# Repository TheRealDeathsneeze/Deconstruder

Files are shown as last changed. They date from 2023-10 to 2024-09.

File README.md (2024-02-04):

# Current Status: Experimental

Deconstruder is a toolhead for the voron v0 utilizing the v0.1 carraige and NF crazy, designed around maximizing rigidity while maintaining a small footprint and low mass. No other hot ends will be supported due to some of the unique features of the NF crazy / mosquito hot end, such as the ability to use four bolts on two different planes to secure the hot end to the toolhead, and the ability to carry a 'fan net' or 'mosquito net' at the bottom of the heatsink frame, as well as the built in 2510 mounting saving a fair amount of weight and space over other options. 

[Bill Of Materials](https://github.com/TheRealDeathsneeze/Deconstruder/blob/main/BOM.md)

[Assembly Instructions](https://github.com/TheRealDeathsneeze/Deconstruder/blob/main/assembly_instructions.md)

[Printing guide](https://github.com/TheRealDeathsneeze/Deconstruder/blob/main/STLs/PRINTING.md)

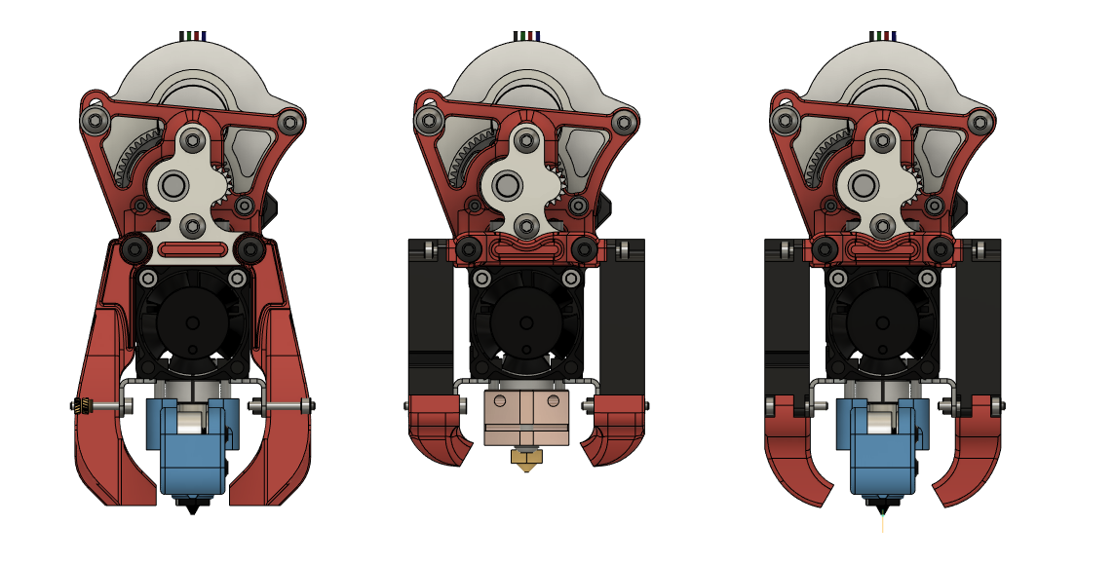
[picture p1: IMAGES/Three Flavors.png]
Deconstruder Types


Deconstruder is the same width in X, and shorter in Z than both mini afterburner and mini stealthburner. It also brings the nozzle higher up with the non-volcano heater block option, this is to aid in center of mass as well as reducing the build volume penalty from switching to a volcano heat block. When used with a standard heat block, the nozzle will be approximately 3mm higher than stock. You may have to adjust the position of your Z rails and endstop for this. 

At this point in time, Deconstruder is very experimental. **Print and install at your own risk.** If you do so, please provide feedback. It would be greatly appreciated and will help the project improve!

CFD has been performed on the SF/HF duct variants

Type 1: Deconstruder HF 
For use with the standard block

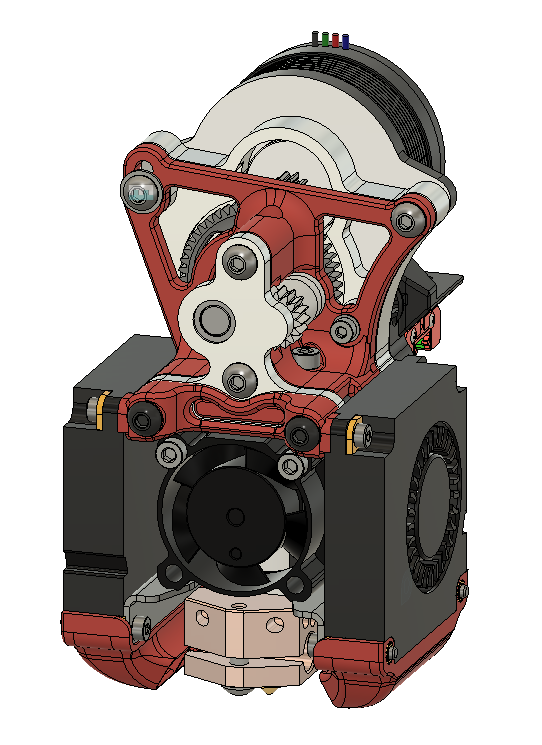
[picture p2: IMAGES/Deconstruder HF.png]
Deconstruder HF


Type 2: Deconstruder UHF
For use with the volcano block

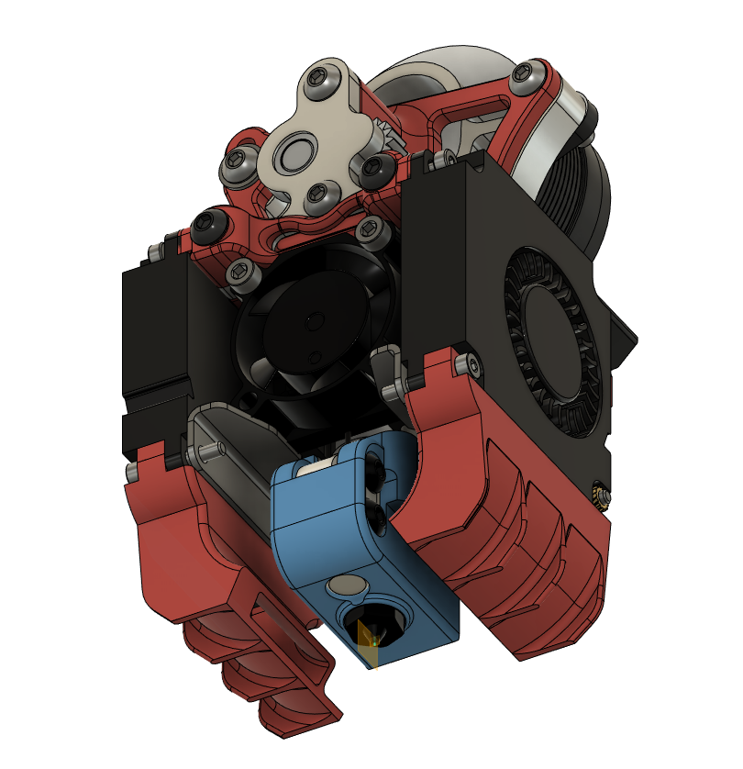
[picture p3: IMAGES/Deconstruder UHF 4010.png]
Deconstruder UHF


Type 3: Deconstruder UHF Sheet Cooling
For use with the volcano block

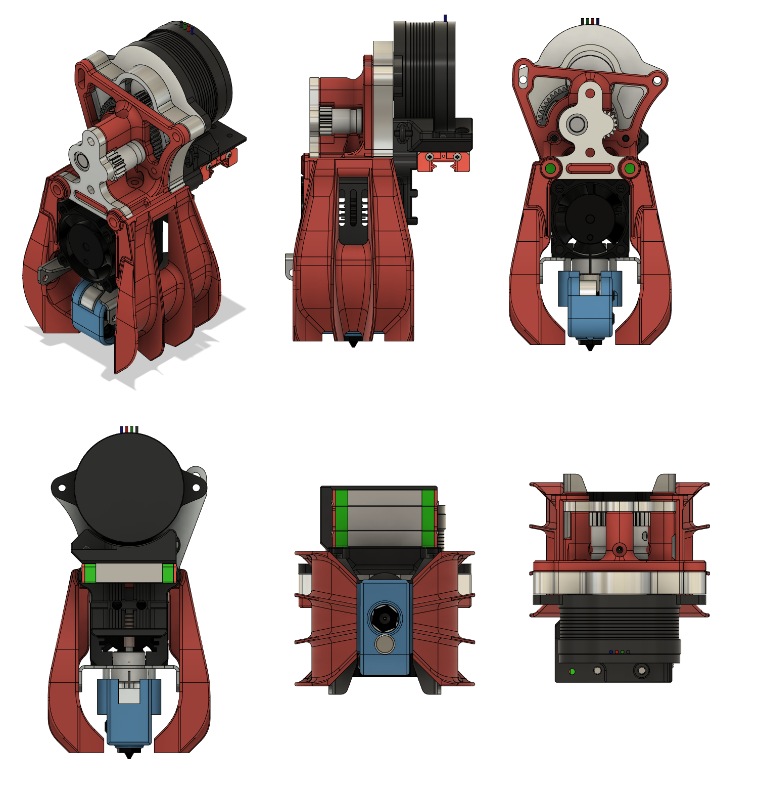
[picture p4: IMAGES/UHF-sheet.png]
Deconstruder UHF Sheet Cooling


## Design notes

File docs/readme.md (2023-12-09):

# Deconstruder

Deconstruder is a toolhead for the Voron V0 utilizing the v0.1 carriage and an NF-Crazy hot end, designed around maximizing rigidity while maintaining a small footprint and low mass. There are currently no plans to support other hot ends due to some of the unique features of the NF-Crazy / Mosquito hot end: the ability to use four bolts on two different planes to secure the hot end to the toolhead, the ability to carry a 'fan net' or 'mosquito net' at the bottom of the heatsink frame and the built-in 2510 fan mount saving a fair amount of weight and space over other options.

Deconstruder Types

Deconstruder is identical in width in the X axis, while being shorter in the Z axis than both the mini AfterBurner and mini StealthBurner. It also brings the nozzle higher up with the non-volcano heater block option to aid in optimizing the center of mass as well as reducing the build volume penalty from switching to a volcano heat block. When used with a standard heat block, the nozzle will sit approximately 3mm higher than stock. You may have to adjust the position of your Z rails and endstop for this.

At this point in time, Deconstruder is very experimental. **Print and install at your own risk.** If you do so, please provide feedback. It would be greatly appreciated and will help the project improve!

Computational fluid dynamics simulations have been performed on the Standard Flow & High Flow duct variants.

## Type 1: High Flow (HF)

For use with the standard block

Deconstruder HF

## Type 2: Ultra-High Flow (UHF)

For use with the volcano block

Deconstruder UHF

## Type 3: Ultra-High Flow (UHF) Sheet Cooling

For use with the volcano block

Deconstruder UHF Sheet Cooling

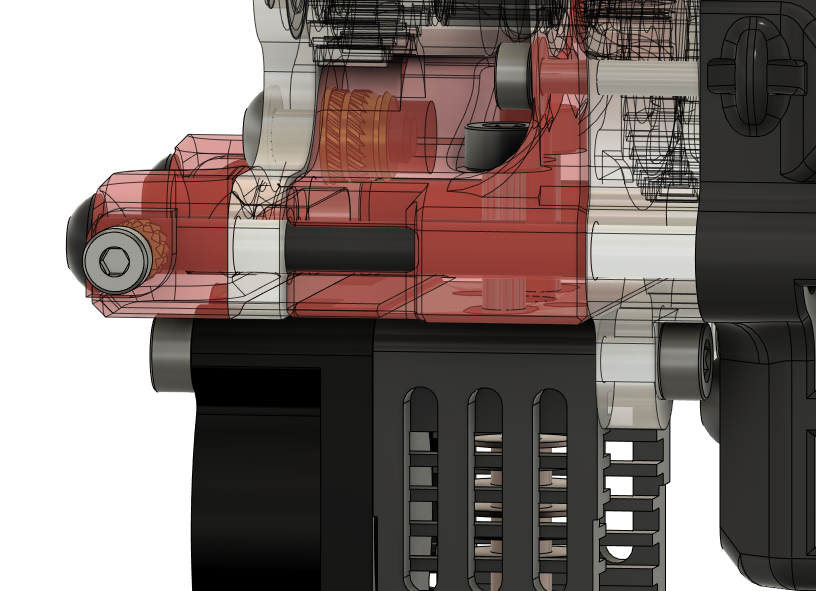
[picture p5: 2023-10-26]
IMAGES/4bolt mains.png

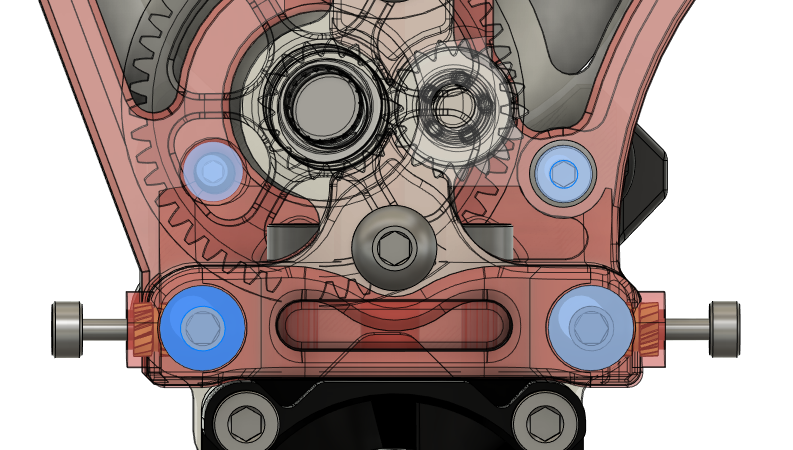
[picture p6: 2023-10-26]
IMAGES/easy-removal.png

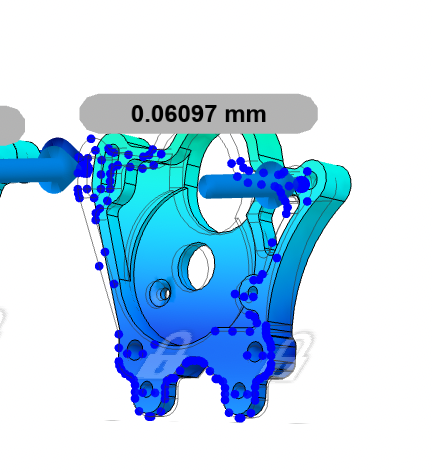
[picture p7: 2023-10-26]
IMAGES/FEA Simulation.png

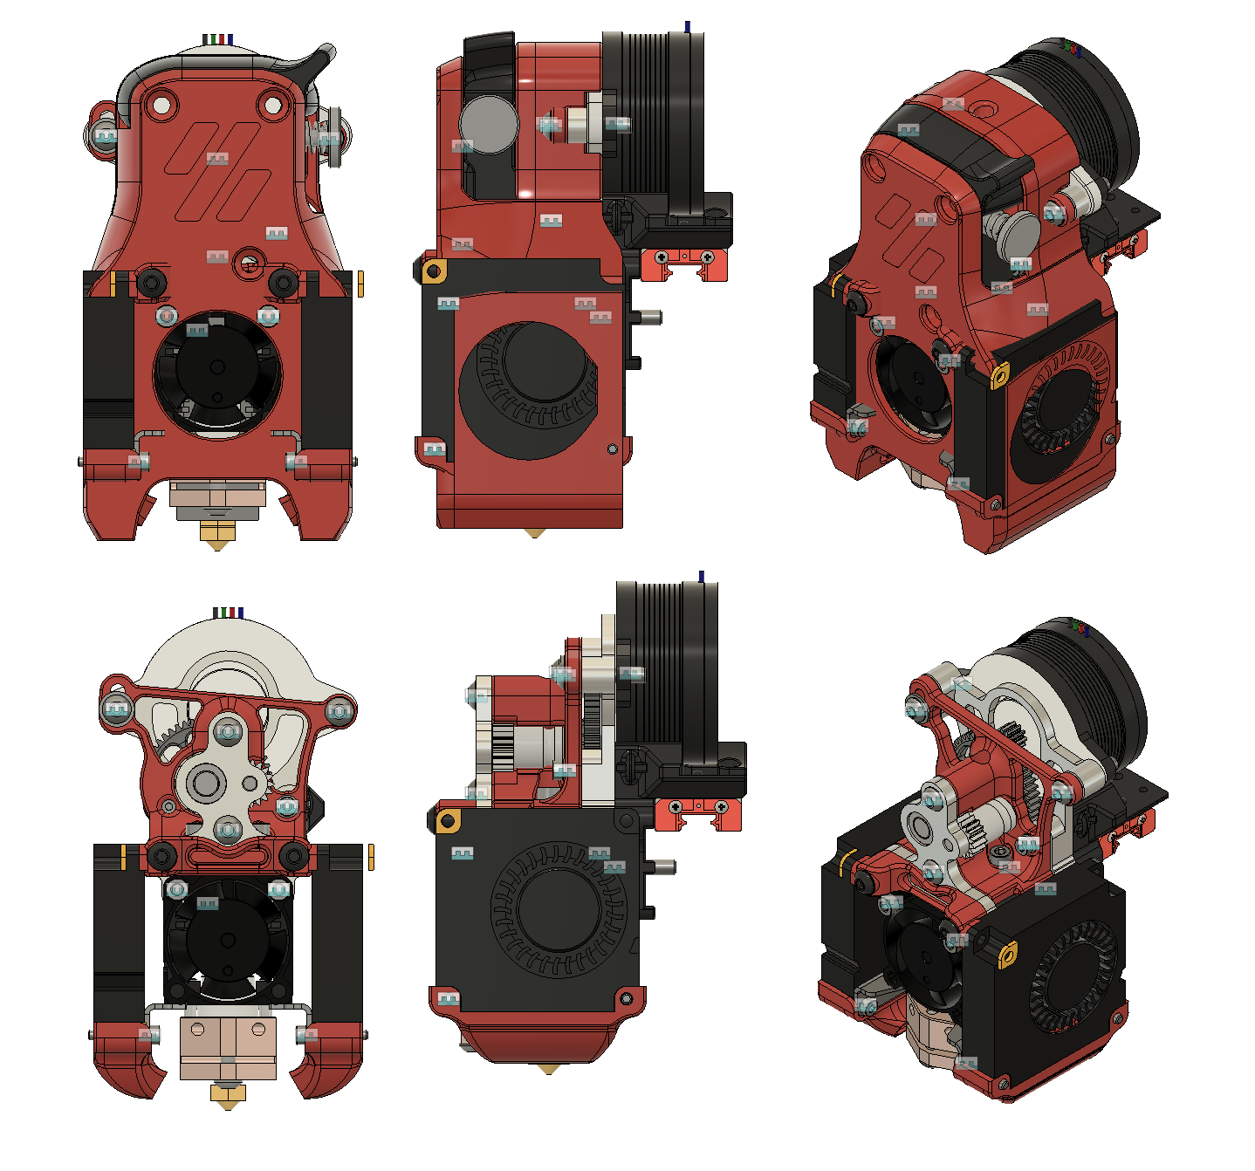
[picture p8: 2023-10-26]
IMAGES/Deconstruder vs MiniAB.png

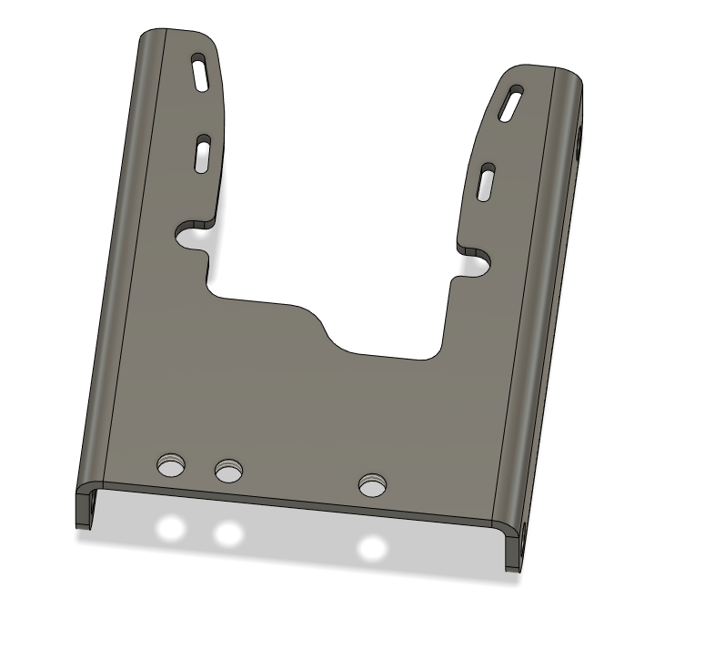
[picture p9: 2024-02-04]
IMAGES/new_fan_net_bent.png

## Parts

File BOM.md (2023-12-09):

UHF sheet

SHCS M2.5 x 14 - 2

SHCS M2.5 x 4 - 2

SHCS M2.5 x 10 - 2

SHCS M2.5 x 8 - 1

BHCS or SHCS M3 x 35 (partially threaded reccomended) - 2

BHCS M3 x 8 - 2

BHCS M3 x 12 - 2 (replace with M3 x 16 if using standoff for toolhead board)

SHCS M2 x 4 - 4

M3x5x4 Heatset insert - 2

M2x4 heatset insert - 4

4010 variants

SHCS M2.5 x 14 - 2

SHCS M2.5 x 4 - 2

SHCS M2.5 x 10 - 2

SHCS M2.5 x 8 - 1

BHCS or SHCS M3 x 40 (partially threaded reccomended) - 2

BHCS M3 x 8 - 2

BHCS M3 x 12 - 2 (replace with M3 x 16 if using standoff for toolhead board)

SHCS M2 x 4 - 4

SHCS M2 x 12 - 4

M2 Hex Nut - 4

M3x5x4 Heatset insert - 2

M2x2 heatset insert - 2

custom v0.1 carraige

M3x5x4 heatset insert - 2

M2x3x2 heatset insert - 2

(need to verify heatset insert sizes.) M3 are standard voron size

Optional: Vibratite VC3 or Loctite 222 thread locking compound

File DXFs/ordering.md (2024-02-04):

Currently the suggested vendor for ordering parts is SendCutSend.

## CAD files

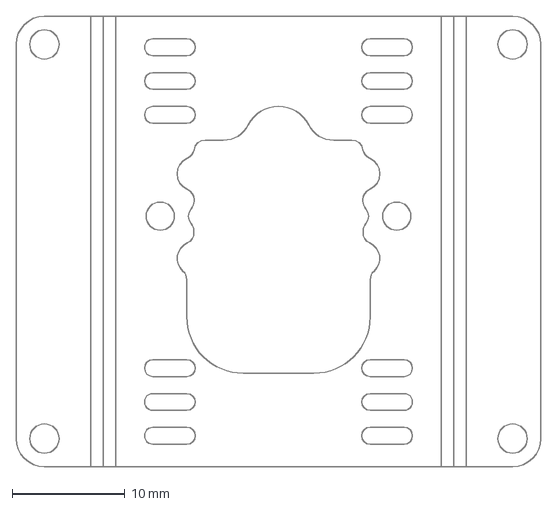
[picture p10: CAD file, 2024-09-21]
DXFs/mosq net.dxf
46.6 x 40.0 mm

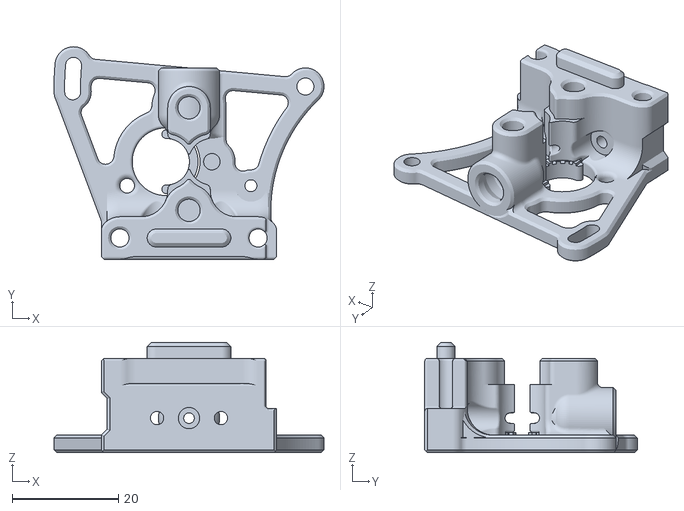
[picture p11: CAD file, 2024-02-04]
STLs/extruder_frame_with_collet_builtin_supports.stl
50.8 x 40.0 x 20.8

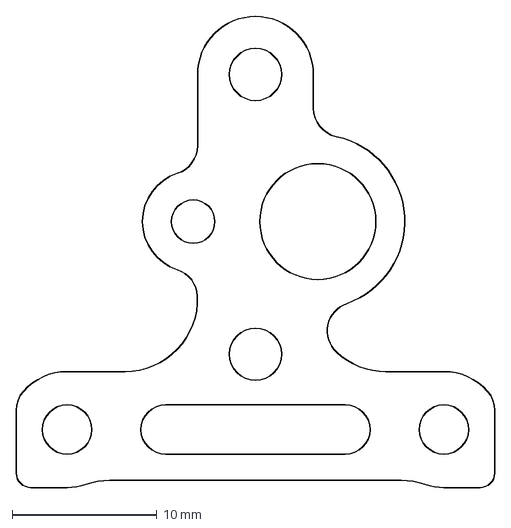
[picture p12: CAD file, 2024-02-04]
DXFs/3.18mm_aluminum_nose_plate.dxf
33.0 x 32.5 mm

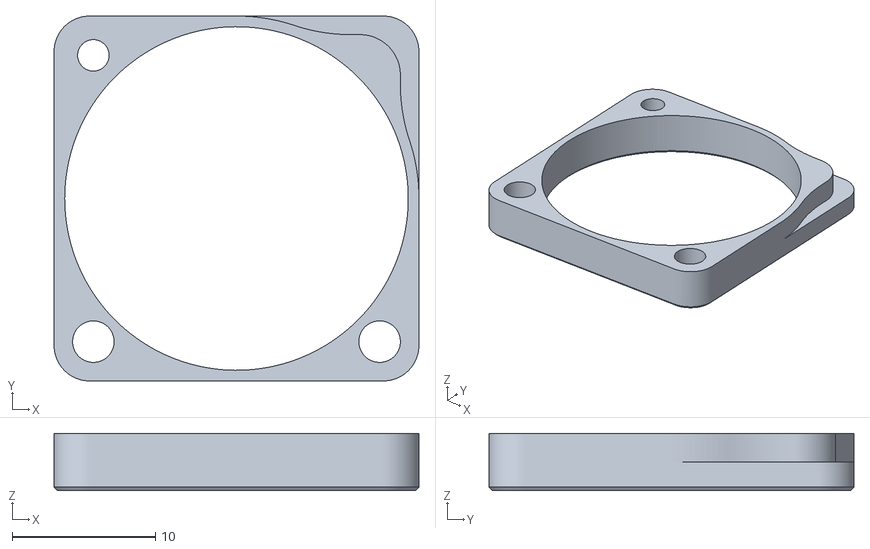
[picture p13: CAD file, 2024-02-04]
STLs/optional_HEF_spacer.stl
25.5 x 25.5 x 4.00

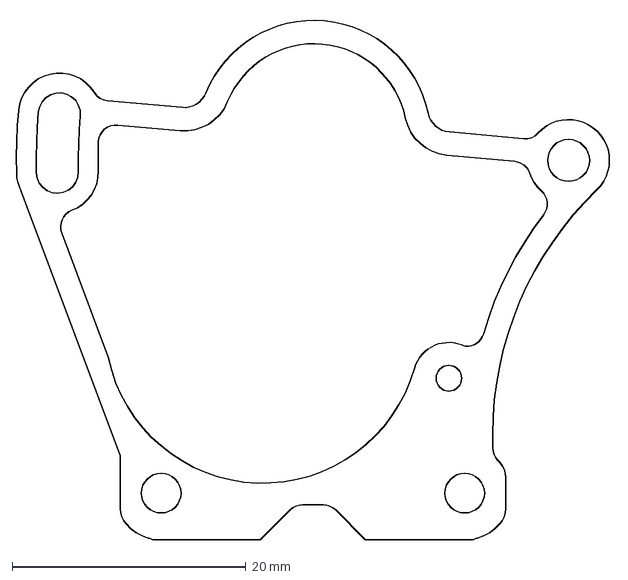
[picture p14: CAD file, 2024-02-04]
DXFs/0.7-0.85mm_shim.dxf
51.0 x 44.9 mm

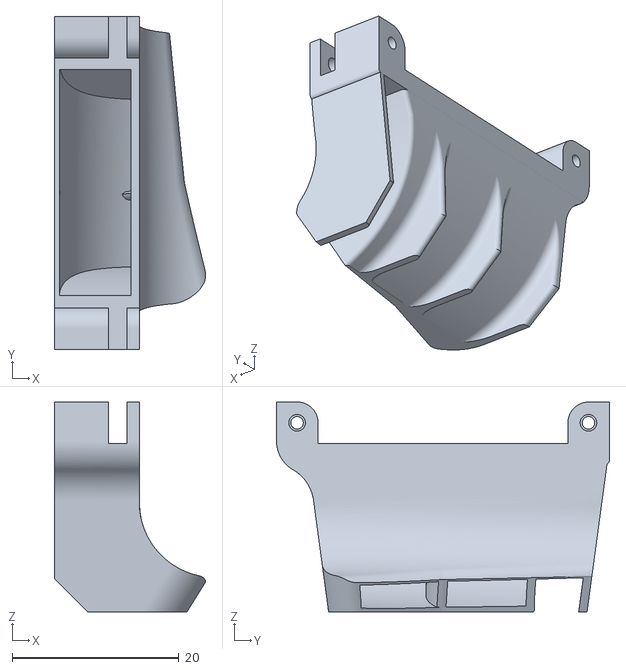
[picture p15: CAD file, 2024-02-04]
STLs/UHF_ductmirror_for_2nd_duct_prints_better_with_supports.stl
18.2 x 40.0 x 25.2

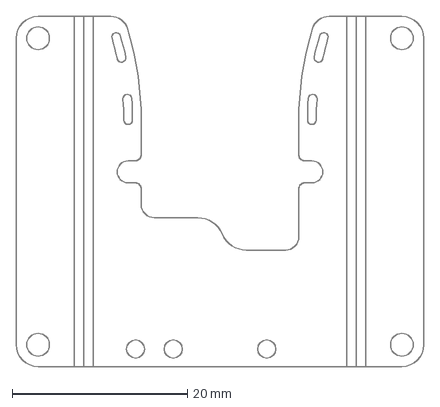
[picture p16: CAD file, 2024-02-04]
DXFs/1mm_titanium_fan_net.dxf
46.6 x 40.0 mm

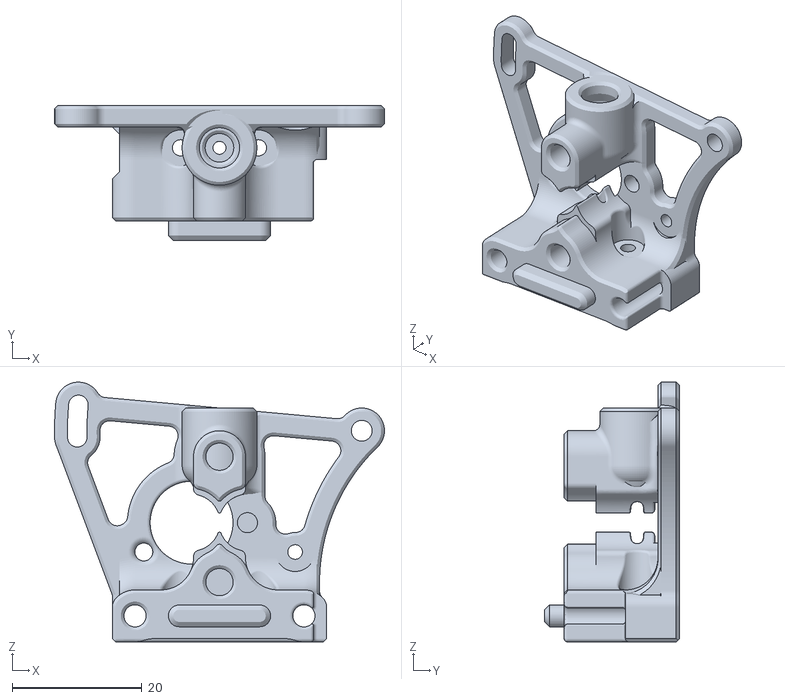
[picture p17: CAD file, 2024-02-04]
STLs/extruder_frame_supports_needed_reorient_as_needed.stl
50.8 x 20.8 x 40.0

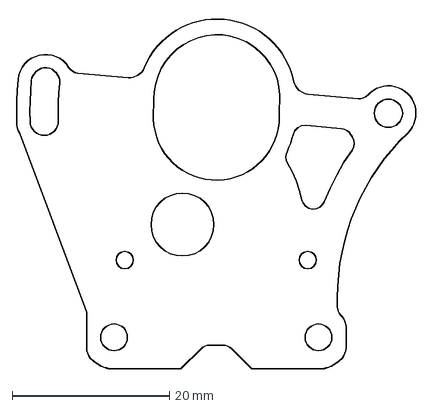
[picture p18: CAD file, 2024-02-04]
DXFs/3.18mm_aluminum_stepper_plate.dxf
51.0 x 44.9 mm

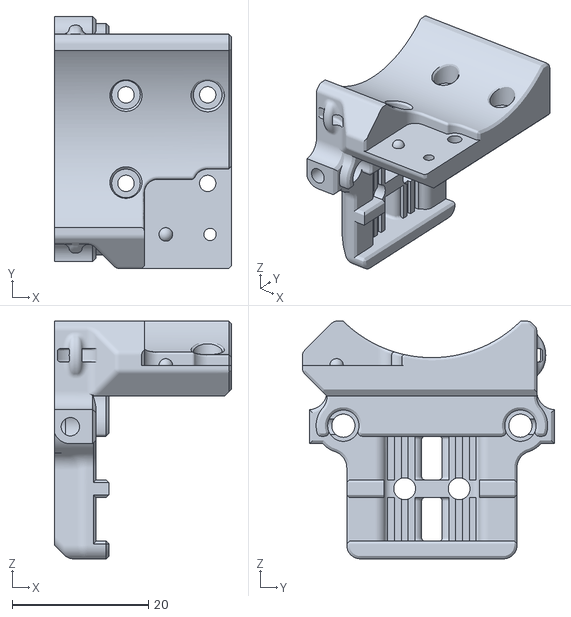
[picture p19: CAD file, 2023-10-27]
STLs/x_carriage_miniaftb_fan_tabbed.stl
26.0 x 37.0 x 34.9

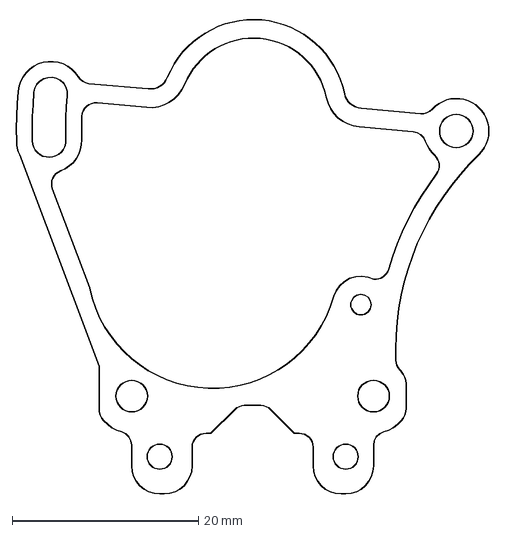
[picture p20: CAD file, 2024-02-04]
DXFs/2.54_aluminum_mid_plate.dxf
51.0 x 51.4 mm

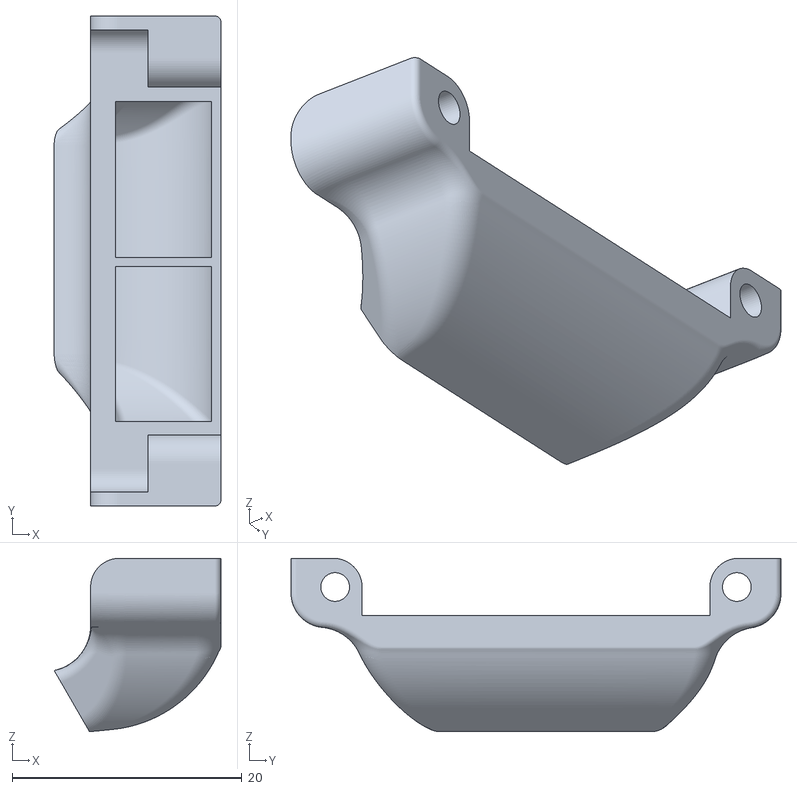
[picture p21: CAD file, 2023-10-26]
STLs/high_fan_duct_v0.1.stl
14.5 x 42.7 x 15.1

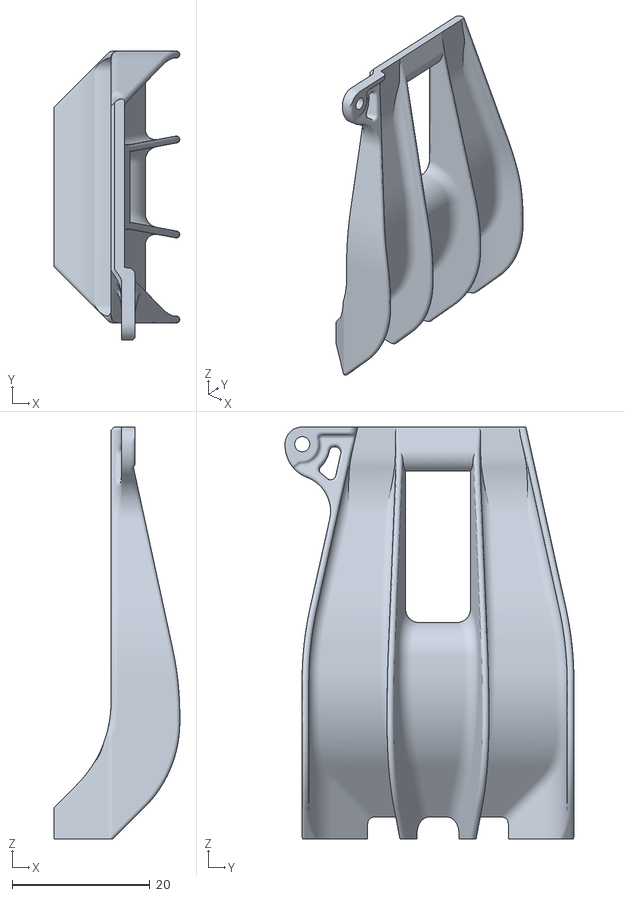
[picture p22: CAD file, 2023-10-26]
STLs/deconstruder sheet director.stl
18.3 x 42.0 x 59.9

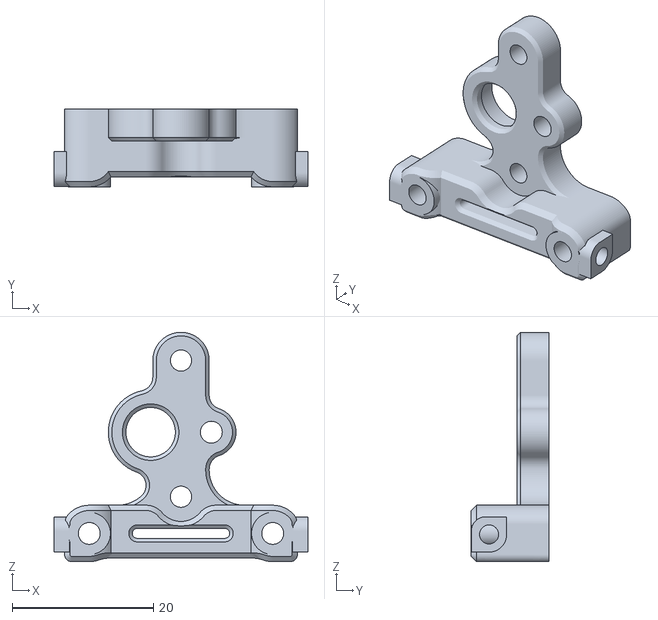
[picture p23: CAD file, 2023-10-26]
STLs/Delta fan plate.stl
36.0 x 11.0 x 32.5

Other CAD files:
STLs/dropped duct .stl
STLs/M3 sheet director.stl
STLs/UHF sheet ribbed.stl
STLs/fan plate.stl
STLs/extruder body.stl
STLs/front plate.stl
STLs/stepper plate.stl

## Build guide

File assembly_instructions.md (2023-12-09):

#assembly instructions#

[note: advise use of vc3 on all fasteners except M2x20 into plastic (optional) for 

##Heatset inserts:##

extruder body: 2x voron standard in front
nose_plate: 2x M2 x 3.2mm heatset inserts. insert after inserting the M3 x 40 SHCS/BHCS
sheet_redirector: 2 x M2 x 3.2mm heatsets. twice. 
modified_carraige: 2: m3 voron standard in front. ignore latch heatset. 2x M2 x 3.2 heatsets. insert after installing M3 heatsets. 

##laser cut variant##

###Caution!### your parts may not be deburred as recieved from your laser cutting supplier if you opted against that option as advised in the sourcing guide. If this is the case they may have sharp edges.  

Inspect parts for defects. Use a file and deburr any sharp edges on exterior features. 

Your laser cut parts will have a very slight taper to the cut (insert picture laser.profile). Keep this in mind when inserting bearings, as they will be easier to install from one side. Be careful to insert the bearings straight (insert picture bearing.insertion) into the nose plate and stepper plates, then use a vice ,two 695 bearings and an M5 bolt and nut, or other tool to press the bearings in until flush with the face (picture using tool)

Insert 2 M2.5x8 SHCS through back of forward_stepper_plate into the hotend but do not fully tighten(picture)

Stack the rear_stepper_plate, printed_shim, and forward_stepper plate together, then insert the 50t gear/shaft assembly. (pic)

Insert ptfe tube into extruder_body, then stack onto assembly. Insert 2x M2.5 x 14 SHCS into hot end. (pic)
stack assembly on Nema14, insert screws. do not fully tighten. (pic)

Tighten all 4 screws for the hot end at this time.(pic)

Press 3mm shaft onto nose plate using printed_tool found in repo. (pic)
Insert idler bearing and idler gear. grease bearings and apply a very light amount of grease to the meshing gears. Do not use too much or it will get onto the filament and ruin your prints!(pic)
Install nose plate, gently wiggling while aligning all parts. 
install 2x M3 x 8 BHCS. Do not fully tighten. 

while rotating the driven side of the BMG gear with your thumb, gently press down on the Nema14 while squeezing the entire assembly with one hand and tightendown the two screws securing the extruder stepper. Check for backlash between the 8t or 10t gear on the stepper and the 50t gear. adjust if needed. Check for free movement of the extruder gears by moving either the driven side or idler side of the BMG gears. You should be able to spin them with a slight amount of resistance from the stepper. Shift the stacked assembly around and adjust backlash as needed. 
Tighten front two screws. 

Congratulations, your extruder and hot end core assembly is complete. You can move onto installing the net and fans/ducts. 

##fan net##
Inspect bends on fan net and ensure they are square. (pic)
gently bend against a table if needed(pic)

If already installed, remove heater block, along witth heatbreak, tubes, and the 2 small screws, being careful not to lose any parts. Be careful, some parts may be loose fitting and want to fall out as you remove assembly! (pic)

Install fan net using 2 M2.5 x 6 SHCS. Note the orientation of the net. Both net types only go on correctly in one orientation (picture)
If using volcano block, install heater cartridge and thermister prior to reinstalling on heatsink. 
Depending on how you choose to route the wires from the heater block, you may want to cut a small notch in the 2510 fan for routing of the thermister wire.
Route the wires through the holes between the heater block and net, and install screws for heatterblock. **DO NOT OVERTIGHTEN, THEY ARE EASY TO STRIP**
Install the 2510 fan and route the wires

##4010 options##

Secure each 4010 fan to the nose plate, then place the ducts onto each fan. Note the orientation of the ducts as they are mirror images of each other.
Secure both fans and cuts to the fan net using M2x10 SHCS, through the inside of the fan net, into a nut on the other side of the duct. use the tip of your finger to hold the nut while starting the screws, being careful not to crossthread it. 
Insert 2 M3 x 40? BHCS and secure toolhead to carraige. 
(optional) insert M2 x 20 through extruder and tighten. Do not overtighten. If using lighteight 50t(or drill a hole through it), you can install 2nd M2 x 20mm through the hole. 
Insert M2 x 6 or M2 x 8 with fan_saver_2mm into nose plate and tighten. Do not overtighten. 
If using optional x_axis_carraige, insert and tighten M2 x 6 ( or M2 x 8 + fan_saver_2mm) 

##sheet redirection##

Secure both sheet redirectors to the fan net using M2 x 6 or M2 x 8mm SHCS using a ball end allen key.
Insert 2 M3 x 35? BHCS and secure toolhead to carraige. 
(optional) insert M2 x 20 through extruder and tighten. Do not overtighten. If using lighteight 50t(or drill a hole through it), you can install 2nd M2 x 20mm through the hole.  

Congratulations. Your toolhead is now assembled.

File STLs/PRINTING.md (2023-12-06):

print extruder parts with standard voron print settings for strength. 0.4mm to 0.5mm nozzle reccomended.
The parts have not been resized for shrinkage.
The ducts have several thin walled sections. I would highly advise printing with a 0.2 to 0.3mm nozzle and using a lower layer height. As a voron V0 can quite easily reach high enough chamber temperatures to make ABS and ASA get a little soft, it would be advisable to print these parts in polycarbonate for higher temperature resistance. Addittionaly, there are files for a CNC version of the nose plate and stepper frame for those that want an even more rigid setup.

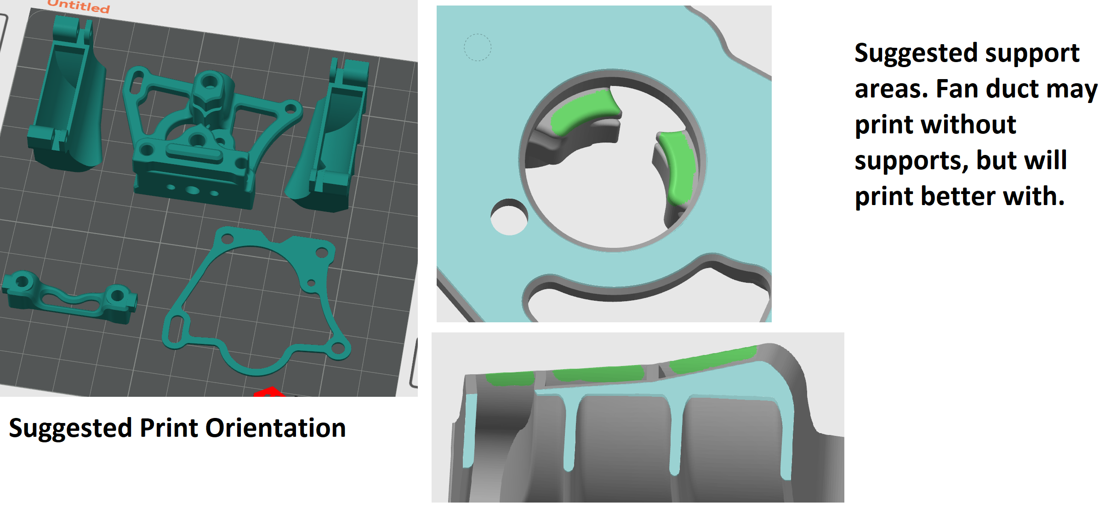
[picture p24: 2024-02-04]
IMAGES/suggest_print_orientation.png

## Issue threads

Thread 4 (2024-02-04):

Heat creep related jamming with ceramic heat break

TheRealDeathsneeze, 2024-02-04:
As of the time of this writing, I have experienced multiple instances where the ceramic heat break of the NF Crazy has not had adequate thermal performance to allow for adequate performance in printers with elevated chamber temperatures. I have experienced these issues at temperatures above 80C for ABS, and 105C for 3DXTech ezPC.

These issues have not occurred with ABS at 75C chamber, or 95-100C chamber with ezPC. Thermal performance has been more than adequate at reduced chamber temperatures, and it is likely that only users that are operating at elevated temperatures will experience this issue.

For now, it is suggested to avoid using the ceramic heat break and instead use the older bimetal copper/stainless heatbreak or the one peice titanium unit.

TheRealDeathsneeze, 2024-02-04:
One possible solution will be to adjust the rear portion of the fan net to allow more area for the exhaust from the hot end fan, which may also assist in wiring management with the hot end and thermistor wires. An updated fan net will be developed, which should also be easier to install as well

HumbleDeer, 2024-07-04:
On what hot end is this exactly? Just a stock setup of an NF Crazy? I may
order parts necessary to measure more closely with a thermocouple. I've got
time to kill, and probably printer parts too.

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

Closed 2024-02-04.

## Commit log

2023-10-26 Add files via upload
    initial prototype STLs
    [Delta fan plate.stl, M3 sheet director.stl, UHF sheet ribbed.stl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]
2023-10-26 Add files via upload
    uploaded Alpha version of CAD, in both .f3d and .step
2023-10-26 Add files via upload
    CFD of hi-SF/HF ducts courtesy of Lorduino.
2023-12-06 Add files via upload
    added new SH/HF duct options for testing.
    Increased size of bearing pockets in printed extruder parts.
2023-12-09 Create assembly_instructions.md
    initial draft for assembly manual
2023-12-09 Move CAD files to Git LFS
2023-12-09 Move & import CAD files to Git LFS
    Using the git lfs command line tools. Also creates a .gitattributes file for this purpose.
    CAD/deconstruder v24.step.7z, CAD/deconstruder v24.f3d, CAD/deconstruder_v25.f3d, CAD/deconstruder_v25.step.7z
2024-09-21 added new fan net
    [mosq net.dxf]
